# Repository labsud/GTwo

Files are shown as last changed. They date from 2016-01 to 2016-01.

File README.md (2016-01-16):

<h1 id="gtwo_shield_for_arduino_due_tinyg_2">GTwo Shield for Arduino DUE &amp; TinyG 2</h1>

<p><a href="https://github.com/synthetos/TinyG">TinyG</a> is a 6 axis motion control system designed by Synthetos for driving CNC, Laser cutters, ans so on. It have been designed to run on Atmel ATxmega192. It&#8217;s a complete system (hard + soft).</p>

<p>Some faeatures : </p>

<ul>
<li>6 axis motion (XYZABC axes)</li>
<li>jerk controlled motion for acceleration planning (3rd order motion planning)</li>
<li>status displays (&#8216;?&#8217; character)</li>
<li>XON/XOFF and RTS/CTS protocol over USB serial</li>
<li>RESTful interface using JSON</li>
</ul>

<p><a href="https://github.com/synthetos/g2">TinyG 2</a> is a TinyG ARM port, also developed by Synthetos, working on Atmel Arm Processors, like the one used on low cost Arduino DUE. That port can be configured for using GRBL shields (Arduino Uno form factor) but unfortunately, pinout is slightly differents, so there&#8217;s no way to have more than 3 motors running. No commands, no emergency stops, spindle or homing&#8230; </p>

<p>GTwo is a shield designed to allow easy use or the port of TinyG with all functionnalities. </p>

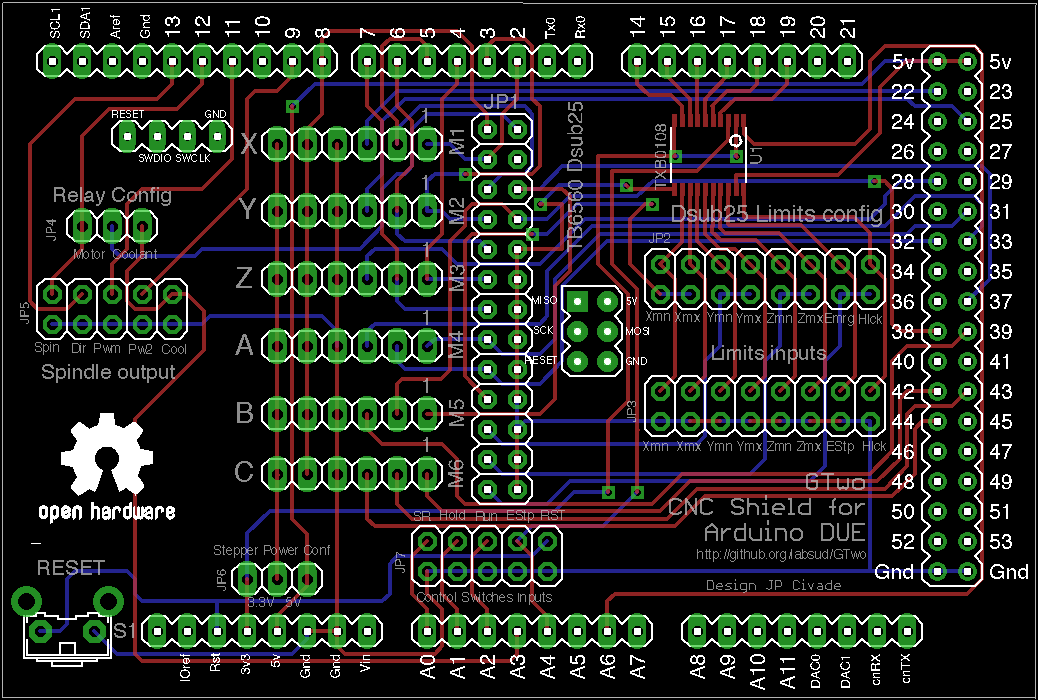
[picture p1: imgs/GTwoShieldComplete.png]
GTwo assembly


<p>That shield can be used :</p>

<ul>
<li>Directly connected to a <a href="https://www.google.fr/search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">TB 6560 &#8220;Red&#8221;</a>, for a maximum of 4 axis (X,Y,Z,A) and 4 GPIO inputs (I.E. homing X,Y,Z and emergency stop)</li>
<li>Connected thru 6 X 6 pins connectors to discrete drivers like Leadshine, Gekko, etc., allowing up to 6 axis (X,Y,Z,A,B,C).</li>
</ul>

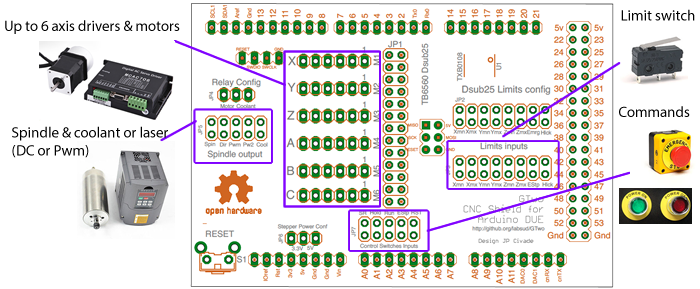
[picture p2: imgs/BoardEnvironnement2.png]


<h4 id="caracteristics">Caracteristics</h4>

<ul>
<li>Mostly passive shield, with all connectors for connecting spindle, PWM Spindle, coolant, homing &amp; Limits, switch for program control, up to 6 axis stepper driver boards</li>
<li>Since DUE is not 5V tolerant, limits inputs are level translated to be used @5V</li>
<li>All other inouts ARE not, and should no be connected to anything else than a 0V. (program control)</li>
</ul>

<h4 id="connections">Connections</h4>

<h5 id="when_using_a_tb6560_power_board_">When using a TB6560 power board :</h5>

That work is the property of Jean-Philippe Civade (jp at civade dot com) and is shared under <a href="licence-CC-By-NC 3.0.txt">Creative Common NonCommercial 3.0</a>

<ul>
<li>JP1 : For connectig to a TB6560 &#8220;Red&#8221; Stepper driver board. A cable must be made with a HE10-26F > DB25F emulating parallel port. If using JP1, don&#8217;t use M1>M6</li>
<li>JP2 : Limits configuration for TB6560. Must be left unequipped if using M1 > M6 connections.</li>
<li>JP4 : Relay config. Must be left unequipped if using M1 > M6 connections.</li>
</ul>

<h5 id="when_using_m1_m6_connections_to_discrete_drivers">When using M1 > M6 connections to discrete drivers</h5>

<ul>
<li>M1 > M6 : Allows to connect up to 6 steppers motors (X/Y/Z/A/B/C). If using M1>M6, don&#8217;t use JP1.</li>
<li>JP3 : Limits inputs. Allow to connect limit and/or homing switches (X-, X+, Y-, Y+, Z-, Z+), emergency stop and optionnaly Hardware interlock. All inputs are 5V tolerant.</li>
<li>JP6 : Stepper power conf </li>
</ul>

<p>M1 to M6 pinout :
* Broche 1 : Step
* Broche 2 : Dir
* Broche 3 : Enable motor (independant enable for each axis)
* Broche 4 : GND
* Broche 5 : Global Enable for all axis
* Broche 6 : VCC (3.3V or 5V depending of JP6) setting</p>

<h5 id="other_connectors_">Other connectors :</h5>

<ul>
<li>JP5 : Spindle &amp; Coolant outputs (3.3V). &#8220;Spindle&#8221; is for Spindle on/off, &#8220;dir&#8221; is for spindle direction (CW/CCW), &#8220;PWM&#8221; is for connecting a PWM spindle, &#8220;PW2&#8221; is an optionnal secondary PWM, &#8220;Cool&#8221; is for connecting cooolant command. </li>
<li>JP7 : Control inputs. Connect swtches for Soft Reset (SR), Feed Hold (Hold), Cycle Start (Run), Emergency Stop (ESTP) or hardware reset (RST)</li>
</ul>

<h5 id="configuration_jumpers_">Configuration Jumpers :</h5>

<p>JP2 : Must be equipped with 4 jumpers allowing to route X- or X+ to Pin 10 of parallel port, Y- or Y+ to pin 11 of parallel port, Z-or Z+ on pin 12 of paralel port, and emergency stop or hardware interlock on pin 13 of parallel port. 
JP4 : Must be equipped with 1 jumper allowing to route motor or coolant to the embedded relay of TB6560 red board.
JP6 : Must be equipped with 1 jumper to route a 3.3V or a 5V to M1 > M6 pin 6.</p>

<h5 id="associated_documents_">Associated Documents :</h5>

<ul>
<li><a href="GTwoShieldSchematics.pdf">Schematics</a></li>
<li><a href="partlist.txt">BOM</a></li>
<li><a href="GTwoShield.zip">ZIP archive for manufacturing</a></li>
<li><a href="imgs/DUE tinyG2 pinout 0.2.pdf">Due Pinout for Tiny G2</a></li>
<li><a href="imgs/GTwoShieldAssembly.pdf">Assembly</a></li>
<li><a href="imgs/GTwoShieldTop.png">Top view</a></li>
<li><a href="imgs/GTwoShieldBottom.png">Bottom view</a></li>
</ul>

<h5 id="example_configuration_">Example configuration :</h5>

<p>This configuration fits to a machine with origin switches at the bottom left ad top Z, for a CNC machine. GTtwo is connected to a TB6560 driver board, and board relay is used to power the spindle. (motor = M3/M5 Gcode). 
TB6560 inputs are Xmin, Ymin, ZMax, Emergency stop. A 3.3V is routed to M1>M6 pin 6.</p>

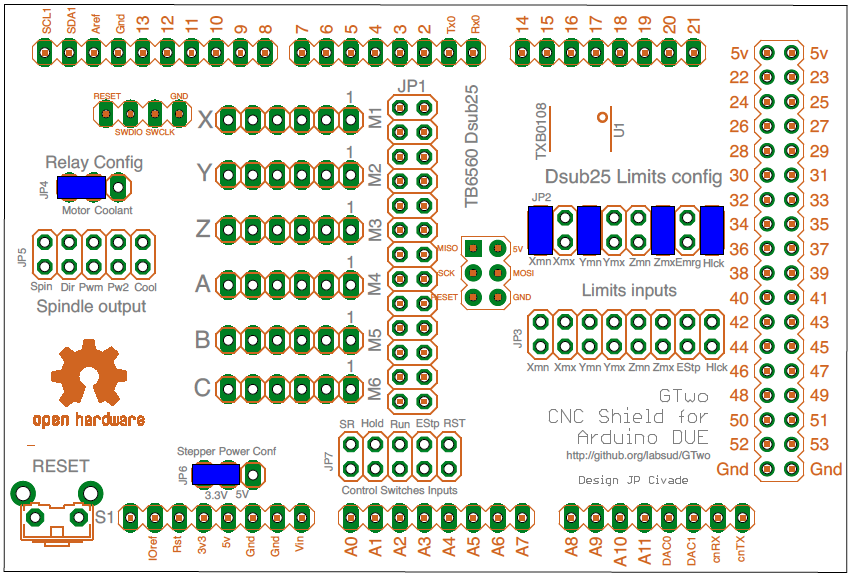
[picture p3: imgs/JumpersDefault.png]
GTwo Default Configuration


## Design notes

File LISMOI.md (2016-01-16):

<h1 id="shield_gtwo_pour_arduino_due_tinyg_2">Shield GTwo pour Arduino DUE &amp; TinyG 2</h1>

Ce travail est la propri&eacute;t&eacute; de Jean-Philippe Civade (jp at civade dot com), et est mis sous licence <a href="licence-CC-By-NC 3.0.txt">Creative Common NonCommercial 3.0</a>

<p><a href="https://github.com/synthetos/TinyG">TinyG</a> est un syst&egrave;me de contr&ocirc;le &agrave; 6 axes d&eacute;velopp&eacute;  par Synthetos pour piloter CNC, d&eacute;coupe laser, etcc. Il a &eacute;t&eacute; con&ccedil;u pour fonctionner sur processeur Atmel ATxmega192.  C&#8217;est un syst&egrave;me complet (hard + soft).</p>

<p>Quelques caract&eacute;ristiques :</p>

<ul>
<li>Gestion de 6 axes (XYZABC)</li>
<li>Planification de mouvement du 3e ordre </li>
<li>Affichage des &eacute;tats (caract&egrave;re &#8216;?&#8217;)</li>
<li>Gestion des protocoles de handshake XON/XOFF &amp; RTS/CTS sur la liaison s&eacute;rie via USB </li>
<li>Interface RESTful utilisant JSON</li>
</ul>

<p><a href="https://github.com/synthetos/g2">TinyG 2</a> est un portage de TinyG sur processeurs ARM, d&eacute;velopp&eacute; &eacute;galement par Synthetos, fonctionnant sur les processeurs ARM d&#8217;Atmel, comme celui utilis&eacute; sur la carte &eacute;conomique Arduino DUE. Ce portage peut &ecirc;tre configur&eacute; pour utilis&eacute; des shields GRBL standard (format Arduino UNO), mais malheureusement pas compl&egrave;tement. En effet, si il est possible de commander les moteurs pas &agrave; pas, tous les autres signaux sont rout&eacute;s sur les connecteurs d&#8217;extension de la l&#8217;Arduino mega, ce qui rend inaccessible les commandes manuelles, de fins ds courses, de commande de broche, etc.. </p>

<p>C&#8217;est pr&eacute;cis&eacute;ment pour rendre accessible tous ces signaux qu&#8217;a &eacute;t&eacute; d&eacute;velopp&eacute; la shield GTwo: Permettre une utilisation facile de TinyG2 avec toutes les fonctionnalit&eacute;s mat&eacute;rielles disponibles. </p>

<p>GTwo assembly</p>

<p>Cette shield peut &ecirc;tre utilis&eacute;e de 2 fa&ccedil;ons :</p>

<ul>
<li>Raccord&eacute;e directement &agrave; une carte de puissance <a href="https://www.google.fr/search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">TB 6560 &#8220;Rouge&#8221;</a>. Cela permet la commande d&#8217;un maximum de 4 axes (X,Y,Z,A) et l&#8217;usage de 4 entr&eacute;es GPIO (exemple : Prise d&#8217;origine machine X,Y,Z et arr&ecirc;t d&#8217;urgence)</li>
<li>Raccord&eacute;e &agrave; des contr&ocirc;leurs d&#8217;axes ind&eacute;pendants (Leadshine, Gekko, etc.,) via des connecteurs &agrave; 6 broches. C&#8217;est dans ce cas jusqu&#8217;&agrave; 6 axes qui peuvent &ecirc;tre pilot&eacute;s (X,Y,Z,A,B,C). Dans ce cas, jusqu&#8217;&agrave; 6 swiches d&#8217;origine machine ou de fin de course peuvent &ecirc;tre raccord&eacute;es.</li>
</ul>

<p>GTwo assembly</p>

<h4 id="caracteristiques">Caracteristiques</h4>

<ul>
<li>Shield principalement passive, avec tous les connecteurs pour connecter broche traditionnelle ou PWM, arrosage, switches de prise d&#8217;origine et de limites, boutons de commande de l&#8217;ex&eacute;cution du programme, et jusqu&#8217;&agrave; 6 axes via des drivers externes.</li>
<li>Du fait que l&#8217;Arduino DUE n&#8217;est pas tol&eacute;rante au 5V (3.3V seulement&#8230;), un level shifter &agrave; 8 canaux est int&eacute;gr&eacute; pour permettre le raccordement des fins de courses en 5V (fins de courses actifs)</li>
<li>Toutes les autres entr&eacute;es (contr&ocirc;le de l&#8217;ex&eacute;cution du programme) sont pr&eacute;vues pour &ecirc;tre raccord&eacute;es au 0V via des interrupteurs et ne devraient jamais &ecirc;tre raccord&eacute;es &agrave; un 5V sous peine de destruction de l&#8217;Arduino DUE.</li>
</ul>

<h4 id="connexions">Connexions</h4>

<h5 id="lorsque_raccorde_une_carte_de_puissance_tb6560_8220rouge8221_">Lorsque raccord&eacute;e &agrave; une carte de puissance TB6560 &#8220;Rouge&#8221; :</h5>

<ul>
<li>JP1 : Raccordement &agrave; l&#8217;entr&eacute;e parall&egrave;le de la carte de puissance TB6560 &#8220;Rouge&#8221; via un cable r&eacute;alis&eacute; avec un connecteur HE10/26 points > Sub D 25 broches femelle. Si ce connecteur est utilis&eacute;, ne pas utiliser M1>M6</li>
<li>JP2 : Configuration des limites pour TB6560. Ne pas &eacute;quiper lors de l&#8217;utilisation de M1 > M6.</li>
<li>JP4 : Configuration du relais de la TB6560. Ne pas &eacute;quiper lors de l&#8217;utilisation de M1 > M6.</li>
</ul>

<h5 id="lorsque_raccorde_des_drivers_moteurs_externes_via_m1_m6">Lorsque raccord&eacute;e &agrave; des drivers moteurs externes via  M1 &agrave; M6</h5>

<ul>
<li>M1 > M6 : Permet de raccorder jusqu&#8217;&agrave; 6 drivers pour moteurs pas &agrave; pas ou servo moteurs (X/Y/Z/A/B/C). Si utilis&eacute;, ne pas utiliser JP1.</li>
<li>JP3 : Entr&eacute;es limites. Permet de raccorder les interrupteurs de d&eacute;tection de prise d&#8217;origine et de limite.(X-, X+, Y-, Y+, Z-, Z+), l&#8217;arr&ecirc;t d&#8217;urgence et l&#8217;interrupteur capot ouvert. Toutes les entr&eacute;es sont compatibles 5V.</li>
<li>JP6 : Configuration de l&#8217;alimentation envoy&eacute;e sur M1>M6 </li>
</ul>

<p>Le brochage des connecteurs M1 &agrave; M6 est le suivant :
* Broche 1 : Pas (Step)
* Broche 2 : Direction (Dir)
* Broche 3 : Activation moteur (Enable, pour chaque moteur)
* Broche 4 : GND
* Broche 5 : Activation globale (Global Enable pour tous les moteurs simultan&eacute;ment)
* Broche 6 : VCC (3.3V ou 5V en fonction de JP6)</p>

<h5 id="autres_connecteurs_">Autres connecteurs :</h5>

<ul>
<li>JP5 : Sortie broche et arrosage (3.3V). &#8220;Spindle&#8221; est pour le M/A broche, &#8220;dir&#8221; est pour le sens de rotation de la broche, &#8220;PWM&#8221; est pour raccorder une broche &agrave; contr&ocirc;le de vitesse en modulation de largeur d&#8217;impulsion, &#8220;PW2&#8221; est un PWM secodaaire  et &#8220;Cool&#8221; est pour raccorder la commande d&#8217;arrosage.</li>
<li>JP7 : Entr&eacute;es de contr&ocirc;le de l&#8217;ex&eacute;cution du programme. Y raccorder des poussoirs pour  le Reset Soft (SR), la suspension du programme, La reprise ou le d&eacute;marrage du programme (Run),l&#8217;arr&ecirc;t d&#8217;urgence (ESTP) ou le reset mat&eacute;riel de la carte (RST)</li>
</ul>

<h5 id="cavaliers_de_configuration">Cavaliers de configuration:</h5>

<p>JP2 : (si utilisation de la TB6560 rouge) Doit &ecirc;tre &eacute;quip&eacute; de 4 cavaliers permettant le routage des switches de prise d&#8217;origine machine  X- ou X+ sur la broche Pin 10 du port parall&egrave;le, Y- ou Y+ &agrave; la broche 11 du port parall&egrave;le, Z-ou Z+ &agrave; la broche 12 du port parall&egrave;le, l&#8217;arr&ecirc;t d&#8217;urgence ou la protection capot ouvert &agrave; la broche 13 du port parall&egrave;le. 
JP4 : (si utilisation de la TB6560 rouge) Doit &ecirc;tre &eacute;quip&eacute; d&#8217;un cavalier permettant de router la commande moteur ou la commande d&#8217;arrosage sur le relais int&eacute;gr&eacute;.
JP6 : (si utilisation des connecteurs M1 &agrave; M6) Doit &ecirc;tre &eacute;quip&eacute; d&#8217;un cavalier permettant d&#8217;envoyer 3.3V ou 5V &agrave; la broche 6 des connecteurs M1 &agrave; M6.</p>

<h5 id="documents_joints_">Documents joints :</h5>

<ul>
<li><a href="GTwoShieldSchematics.pdf">Sch&eactute;ma de principe</a></li>
<li><a href="partlist.txt">Nomenclature</a></li>
<li><a href="GTwoShield.zip">Archive Zip pour la fabrication</a></li>
<li><a href="imgs/DUE tinyG2 pinout 0.2.pdf">Brochage de la Due avec Tiny G2</a></li>
<li><a href="imgs/GTwoShieldAssembly.pdf">Assemblage</a></li>
<li><a href="imgs/GTwoShieldTop.png">Dessus</a></li>
<li><a href="imgs/GTwoShieldBottom.png">Dessous</a></li>
</ul>

<h5 id="exemple_de_configuration">Exemple de configuration:</h5>

<p>Cette configuration correspond &agrave; une machine dont les swiches d&#8217;origine sont en bas &agrave; gauche et en haut du Z, pour une machine de CNC. GTtwo est dans ce cas raccord&eacute;e &agrave; une carte de puissance TB6560 &#8220;rouge&#8221; dont le relais est utilis&eacute; pour commander le M/A d&#8217;une broche  (moteur on /off = Commandes Gcode M3/M5). 
Les entr&eacute;es de la TB6560 sont respectivement raccord&eacute;es &agrave; Xmin, Ymin, ZMax et un bouton d&#8217;arr&ecirc;t d&#8217;urgence. Une alimentation 3.3V is rout&eacute;e vers la broche 6 des connecteurs M1 &agrave; M6 qui sont inutilis&eacute;s.</p>

<p>GTwo Default Configuration</p>

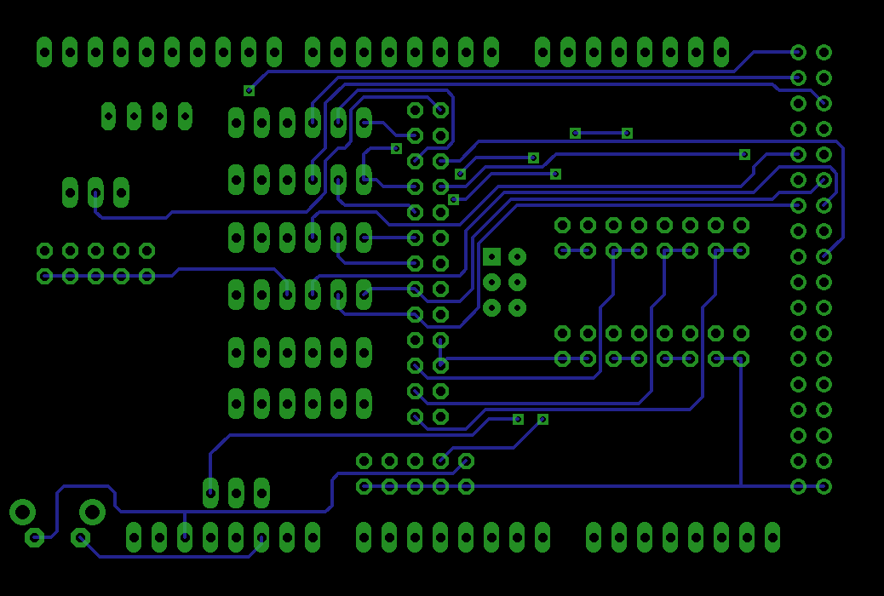
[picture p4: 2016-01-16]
imgs/GTwoShieldBottom.png

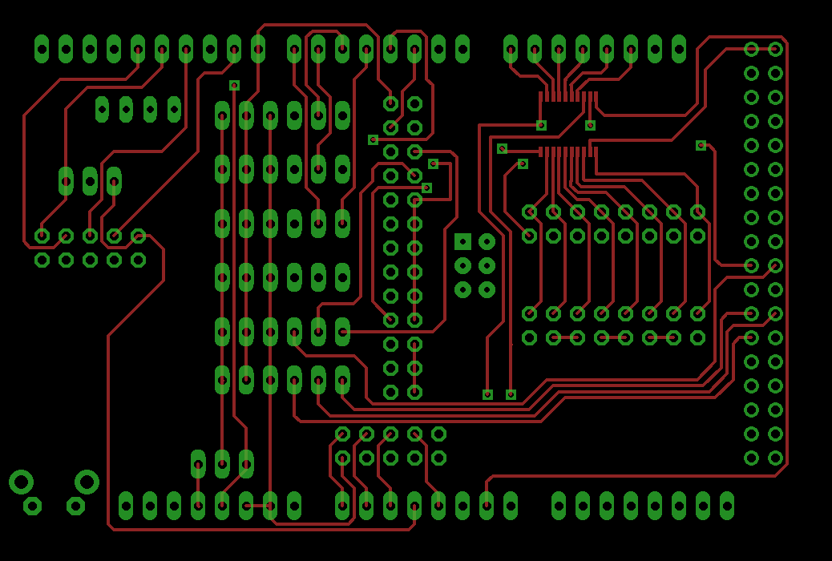
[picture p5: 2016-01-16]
imgs/GTwoShieldTop.png

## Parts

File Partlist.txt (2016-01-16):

Part     Value                   Package     Library      Position (inch)       Orientation

JP1      Header 2 rows           2X13        pinhead      (1.9 1.575)           R270
JP2      Header 2 rows           2X08        pinhead      (2.775 1.675)         R0
JP3      Header 2 rows           2X08        pinhead      (2.775 1.25)          R0
JP4      Header 1 row            1X03        pinhead      (0.6 1.85)            R0
JP5      Header 2 rows           2X05        pinhead      (0.6 1.575)           R0
JP6      Header 1 row            1X03        pinhead      (1.15039998 0.675)    R180
JP7      Header 2 rows     	   2X05        pinhead      (1.85 0.75)           R0
M1       Header 1 row            1X06        pinhead      (1.4 2.125)           R180
M2       Header 1 row            1X06        pinhead      (1.4 1.9)             R180
M3       Header 1 row            1X06        pinhead      (1.4 1.675)           R180
M4       Header 1 row            1X06        pinhead      (1.4 1.45)            R180
M5       Header 1 row            1X06        pinhead      (1.4 1.225)           R180
M6       Header 1 row            1X06        pinhead      (1.4 1.025)           R180
S1       Pushbutton              B3F-31XX    adafruit     (0.45 0.55)           R0
U1       TXB0108                 TSSOP20                  (2.58810002 2.08770005)

6 X 2.54mm Jumpers
1 X HE10 26 pins (TB6560 option)
1 X DB25 Femelle (TB6560 Option)
1 X 5cm 26 pin ribbon

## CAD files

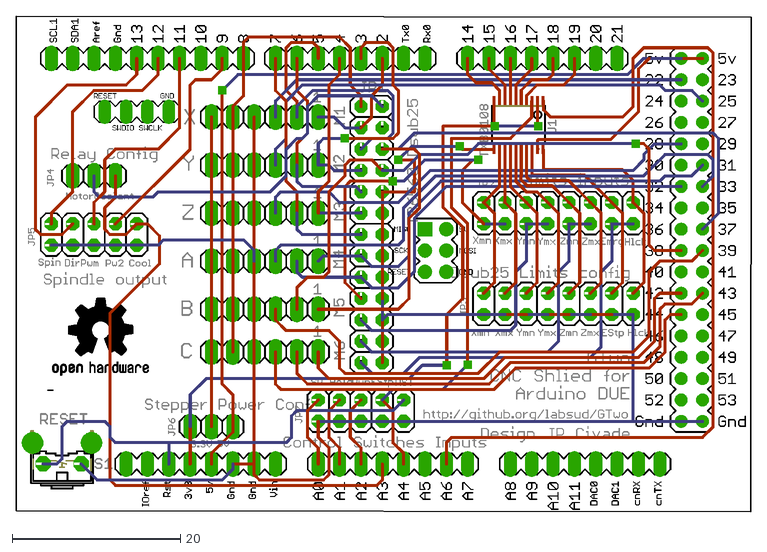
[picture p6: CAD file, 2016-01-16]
GTwoShield.dxf
87.4 x 58.9

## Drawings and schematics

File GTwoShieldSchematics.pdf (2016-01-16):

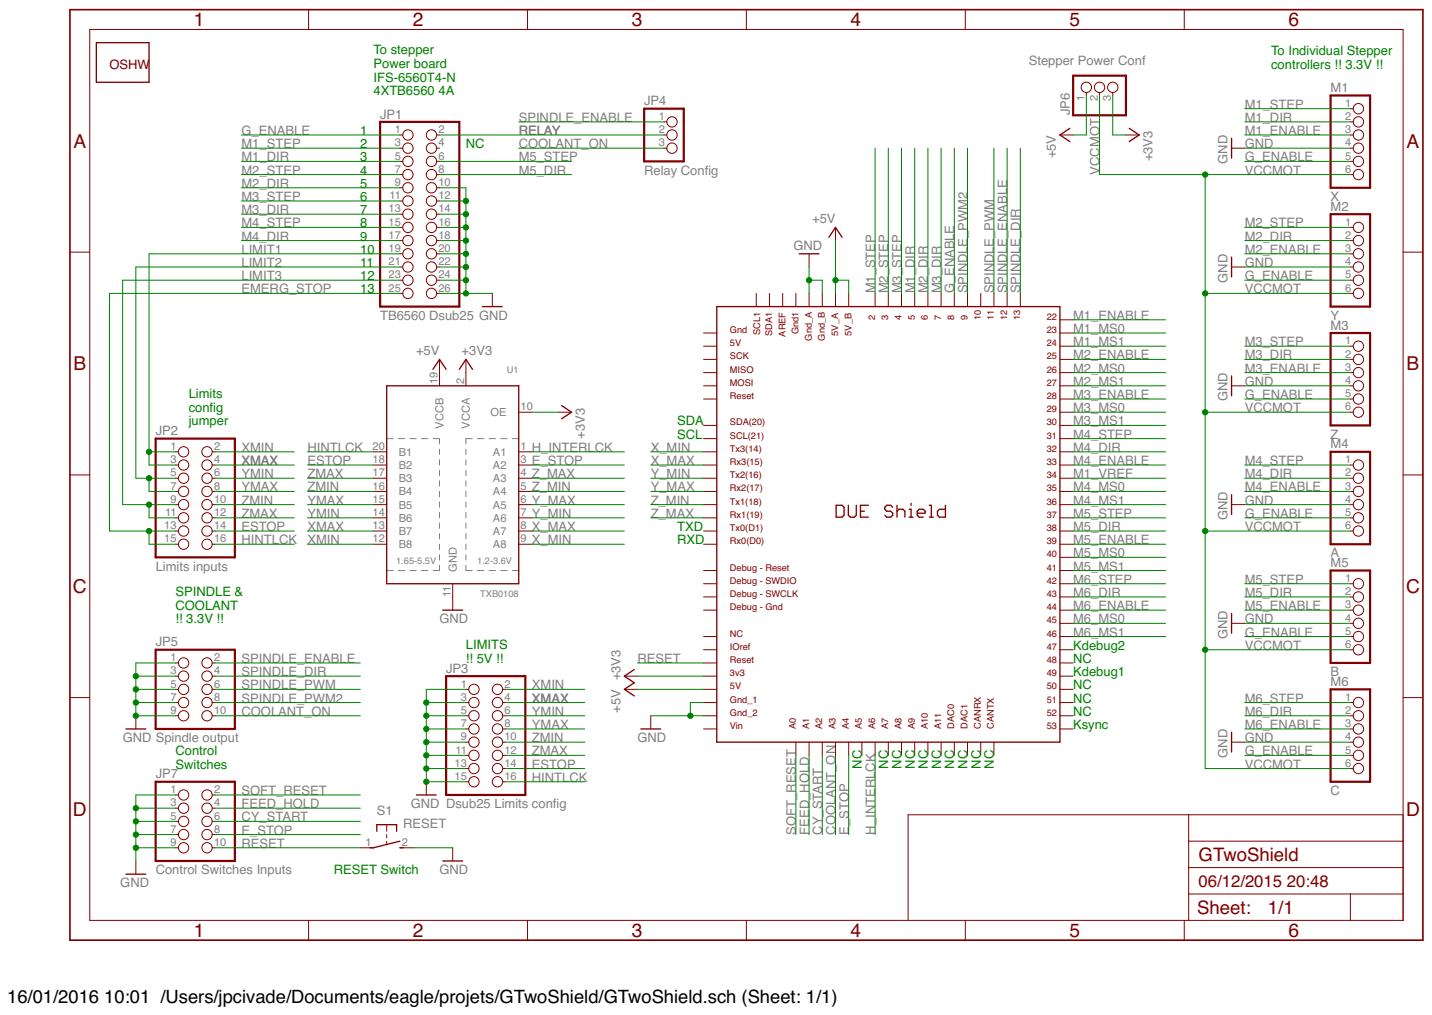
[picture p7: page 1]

To stepper Power board

To Individual Stepper controllers !! 3.3V !!

GND GND GND GND GND

SDA1 SCL1 Debug - Reset Debug - Gnd Debug - SWDIO
5VGnd

16/01/2016 10:01 /Users/jpcivade/Documents/eagle/projets/GTwoShield/GTwoShield.sch (Sheet: 1/1)

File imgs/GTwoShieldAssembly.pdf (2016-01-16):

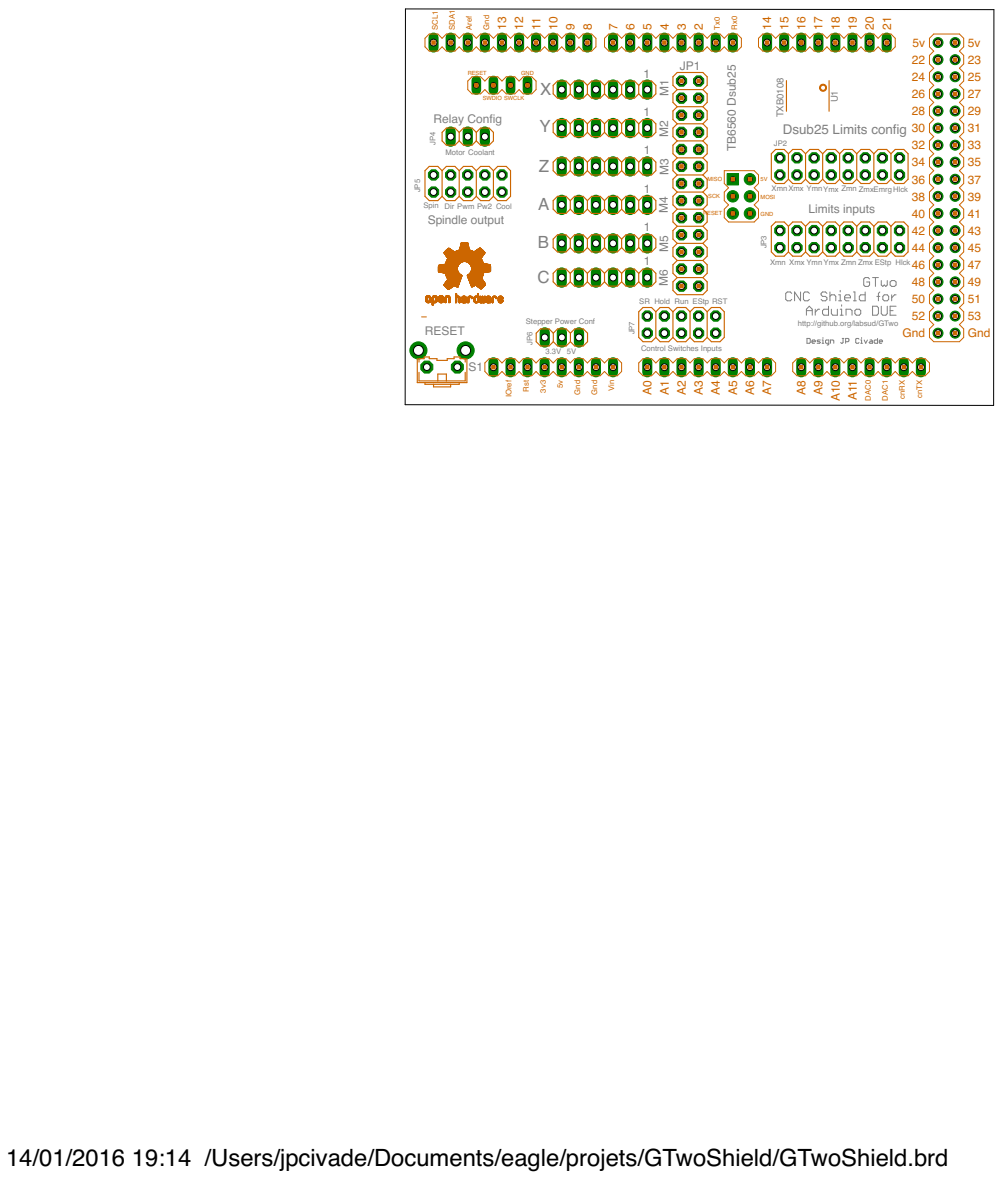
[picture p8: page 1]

5VGND
XmnXmx YmnYmx Zmn ZmxEmrg

SR Hold Run EStp RST

Stepper Power Conf RESET

http://github.org/labsud/GTwo

14/01/2016 19:14 /Users/jpcivade/Documents/eagle/projets/GTwoShield/GTwoShield.brd

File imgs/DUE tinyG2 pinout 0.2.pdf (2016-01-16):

# tinyG2 add-on WIP

# tinyG2

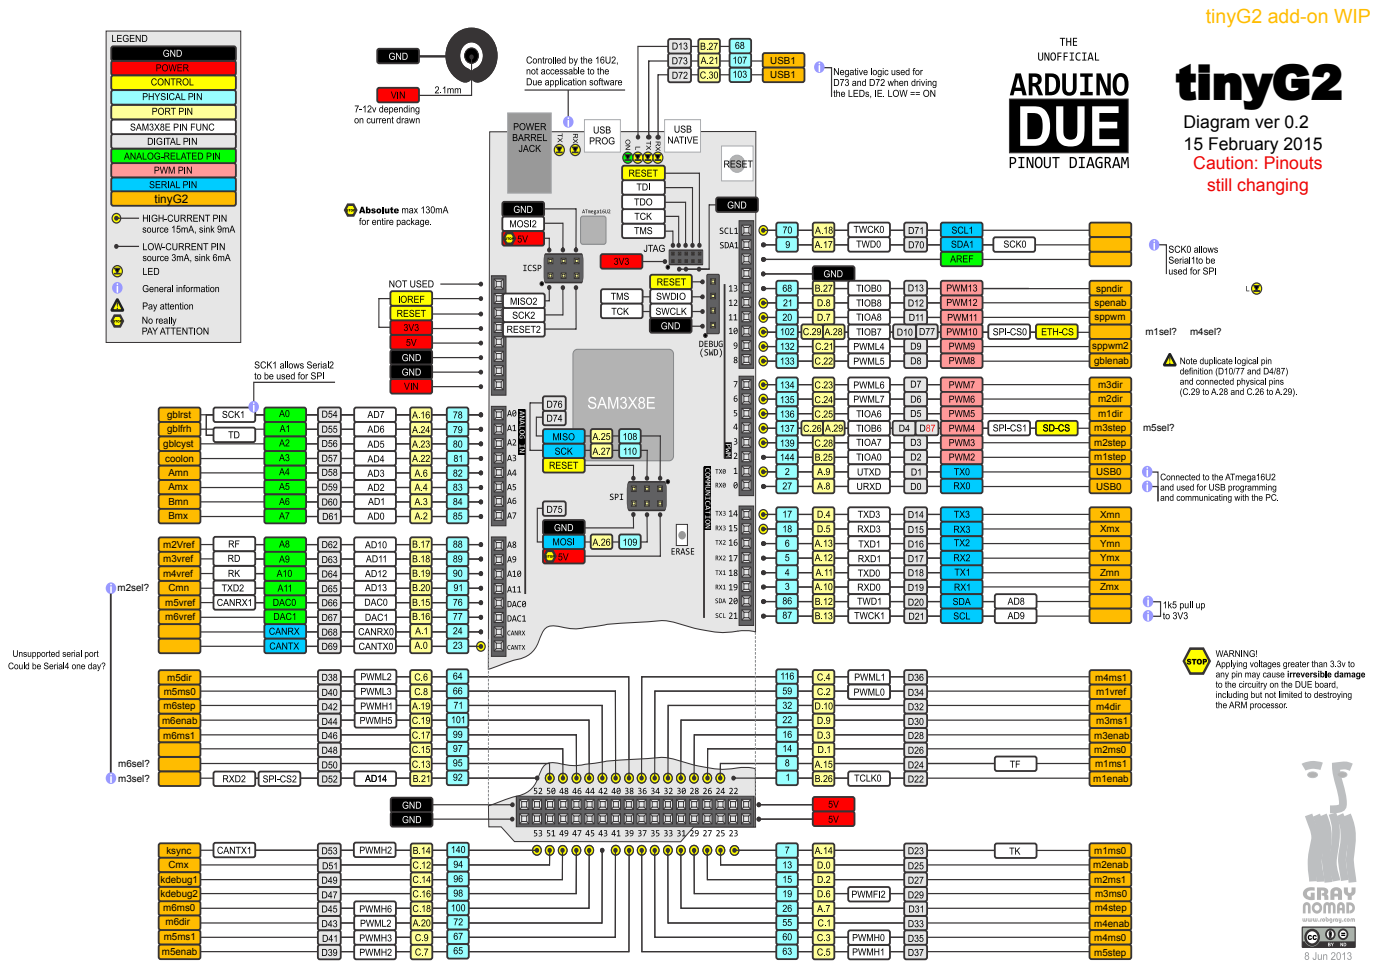
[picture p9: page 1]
Xmn Xmx Ymn Ymx Zmn Zmx; Amn Amx Bmn Bmx; Cmx; Cmn; gblrst gblfrh gblcyst coolon; m2Vref m3vref m4vref; m5vref m6vref; m5dir m5ms0 m6step m6enab m6ms1; m6sel? m3sel?; spndir spenab sppwm; m1sel?; sppwm2 gblenab; m3dir m2dir m1dir m3step m2step m1step USB0; m4ms1 m1vref m4dir m3ms1 m3enab m2ms0 m1ms1 m1enab; m1ms0 m2enab m2ms1 m3ms0 m4step m4enab m4ms0 m5step; m2sel?; m4sel?; m5sel?; m5enab; m6dir; kdebug2; kdebug1; ksync; USB0; USB1 USB1; tinyG2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

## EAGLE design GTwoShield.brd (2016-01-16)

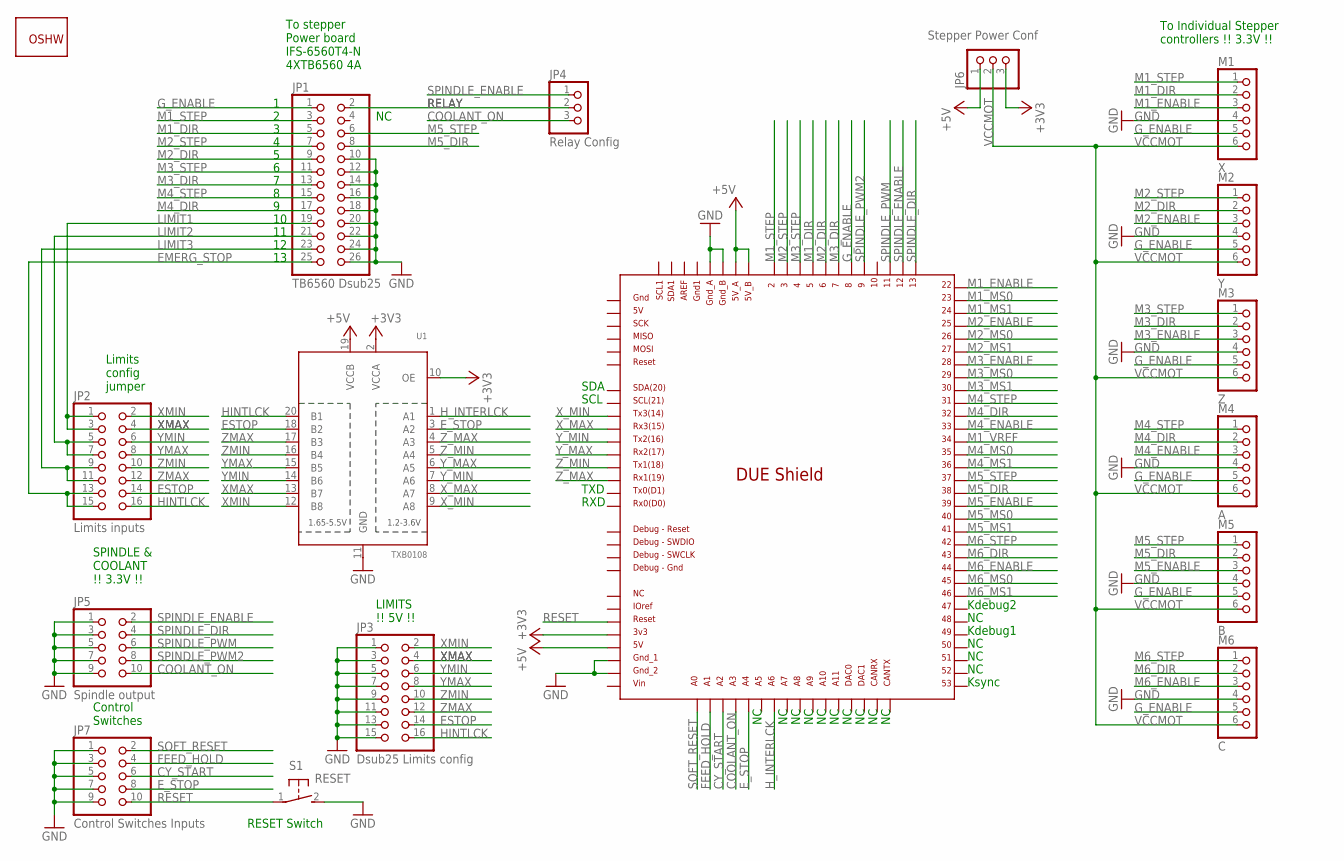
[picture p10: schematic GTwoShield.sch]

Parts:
GOLD_ORB_SM1: OSHWLOGO_GOLD_ORB_MED; OSHW1
JP1: TB6560 Dsub25; 2X13
JP2: Limits inputs; 2X08
JP3: Dsub25 Limits config; 2X08
JP4: Relay Config; 1X03
JP5: Spindle output; 2X05
JP6: Stepper Power Conf; 1X03
JP7: Control Switches Inputs; 2X05
M1: X; 1X06
M2: Y; 1X06
M3: Z; 1X06
M4: A; 1X06
M5: B; 1X06
M6: C; 1X06
S1: RESET; B3F-31XX
U1: TXB0108; TSSOP20
U$1: DUE(NORMAL)

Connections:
+3V3: JP6.3, U1.2 (VCCA), U1.10 (OE), U$1.3V3
+5V: JP6.1, U1.19 (VCCB), U$1.5V, U$1.5V_A, U$1.5V_B
COOLANT_ON: JP4.3, JP5.10, U$1.A3
CY_START: JP7.6, U$1.A2
EMERG_STOP: JP1.25, JP2.13, JP2.15
ESTOP: JP2.14, JP3.14, U1.18 (B2)
E_STOP: JP7.8, U1.3 (A2), U$1.A4
FEED_HOLD: JP7.4, U$1.A1
GND: JP1.10, JP1.12, JP1.14, JP1.16, JP1.18, JP1.20, JP1.22, JP1.24, JP1.26, JP3.1, JP3.3, JP3.5, JP3.7, JP3.9, JP3.11, JP3.13, JP3.15, JP5.1, JP5.3, JP5.5, JP5.7, JP5.9, JP7.1, JP7.3, JP7.5, JP7.7, JP7.9, M1.4, M2.4, M3.4, M4.4, M5.4, M6.4, S1.2 (S), U1.11 (GND), U$1.GND_1, U$1.GND_2, U$1.GND_A, U$1.GND_B
G_ENABLE: JP1.1, M1.5, M2.5, M3.5, M4.5, M5.5, M6.5, U$1.8
HINTLCK: JP2.16, JP3.16, U1.20 (B1)
H_INTERLCK: U1.1 (A1), U$1.A6
LIMIT1: JP1.19, JP2.1, JP2.3
LIMIT2: JP1.21, JP2.5, JP2.7
LIMIT3: JP1.23, JP2.9, JP2.11
M1_DIR: JP1.5, M1.2, U$1.5
M1_ENABLE: M1.3, U$1.22
M1_MS0: U$1.23
M1_MS1: U$1.24
M1_STEP: JP1.3, M1.1, U$1.2
M1_VREF: U$1.34
M2_DIR: JP1.9, M2.2, U$1.6
M2_ENABLE: M2.3, U$1.25
M2_MS0: U$1.26
M2_MS1: U$1.27
M2_STEP: JP1.7, M2.1, U$1.3
M3_DIR: JP1.13, M3.2, U$1.7
M3_ENABLE: M3.3, U$1.28
M3_MS0: U$1.29
M3_MS1: U$1.30
M3_STEP: JP1.11, M3.1, U$1.4
M4_DIR: JP1.17, M4.2, U$1.32
M4_ENABLE: M4.3, U$1.33
M4_MS0: U$1.35
M4_MS1: U$1.36
M4_STEP: JP1.15, M4.1, U$1.31
M5_DIR: JP1.8, M5.2, U$1.38
M5_ENABLE: M5.3, U$1.39
M5_MS0: U$1.40
M5_MS1: U$1.41
M5_STEP: JP1.6, M5.1, U$1.37
M6_DIR: M6.2, U$1.43
M6_ENABLE: M6.3, U$1.44
M6_MS0: U$1.45
M6_MS1: U$1.46
M6_STEP: M6.1, U$1.42
RELAY: JP1.2, JP4.2
RESET: JP7.10, S1.1, U$1.RESET
SOFT_RESET: JP7.2, U$1.A0
SPINDLE_DIR: JP5.4, U$1.13
SPINDLE_ENABLE: JP4.1, JP5.2, U$1.12
SPINDLE_PWM: JP5.6, U$1.11
SPINDLE_PWM2: JP5.8, U$1.9
VCCMOT: JP6.2, M1.6, M2.6, M3.6, M4.6, M5.6, M6.6
XMAX: JP2.4, JP3.4, U1.13 (B7)
XMIN: JP2.2, JP3.2, U1.12 (B8)
X_MAX: U1.8 (A7), U$1.RX3
X_MIN: U1.9 (A8), U$1.TX3
YMAX: JP2.8, JP3.8, U1.15 (B5)
YMIN: JP2.6, JP3.6, U1.14 (B6)
Y_MAX: U1.6 (A5), U$1.RX2
Y_MIN: U1.7 (A6), U$1.TX2
ZMAX: JP2.12, JP3.12, U1.17 (B3)
ZMIN: JP2.10, JP3.10, U1.16 (B4)
Z_MAX: U1.4 (A3), U$1.RX1
Z_MIN: U1.5 (A4), U$1.TX1

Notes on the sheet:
Kdebug2
Kdebug1
Ksync
SDA
SCL
TXD
RXD
To stepper Power board IFS-6560T4-N 4XTB6560 4A
Limits config jumper
To Individual Stepper controllers !! 3.3V !!
SPINDLE & COOLANT !! 3.3V !!
Control Switches
RESET Switch
LIMITS !! 5V !!

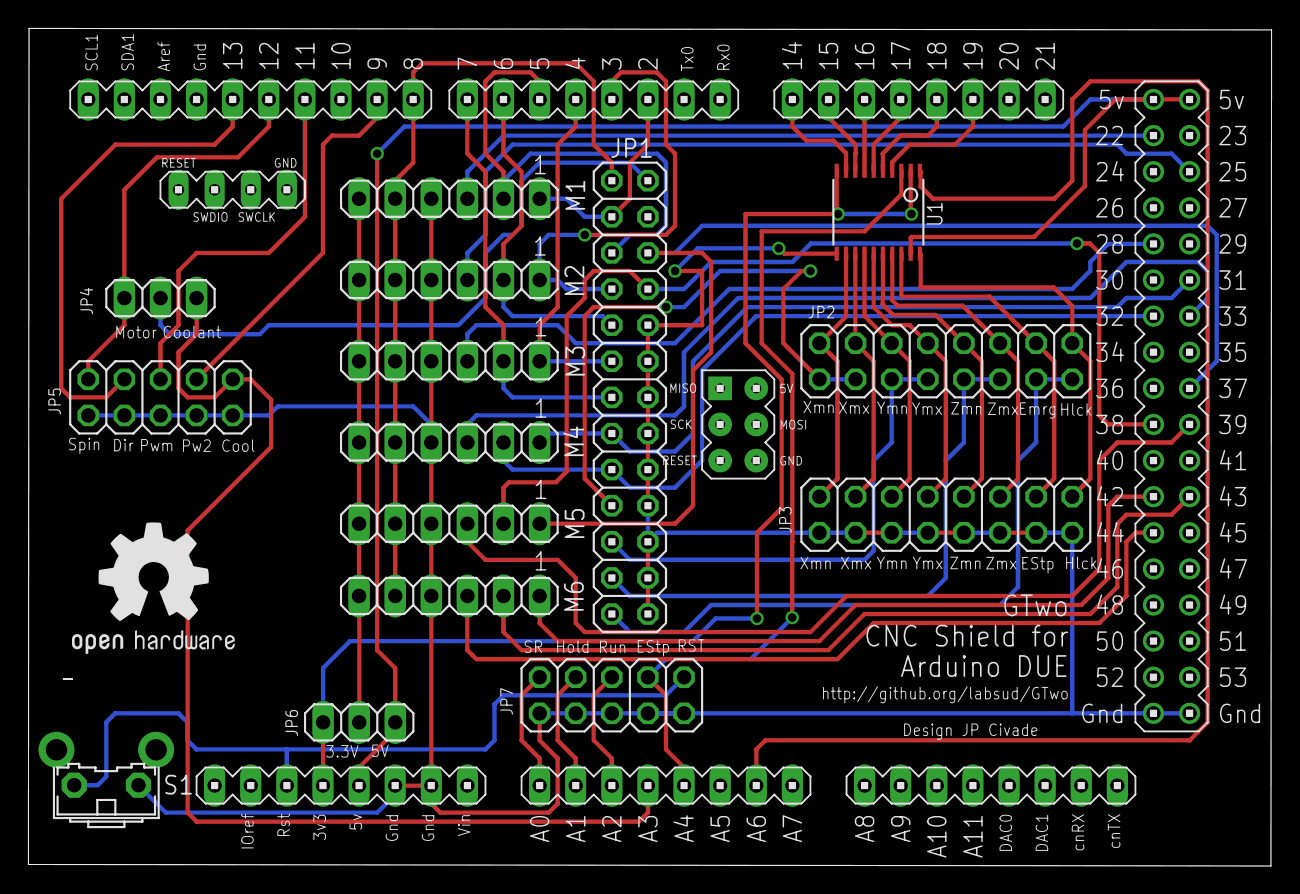
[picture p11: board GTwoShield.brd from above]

Board: 2 copper layers, 87.4 x 58.9 mm, 17 parts (0 on the bottom side), 53 nets.

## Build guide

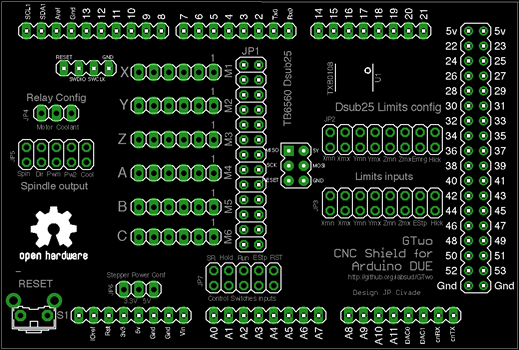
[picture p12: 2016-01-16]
imgs/GTwoShieldAssembly2.png

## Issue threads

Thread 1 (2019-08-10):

Thank you!

norru, 2019-08-10:
Hi @labsud,

I am trying to build my own CNC machine as a semicustom WorkBee design using the Due and g2core.

I was thinking of designing my own from scratch but found your work here instead, which looks like an awesome starting point.

I am planning to use inexpensive TB6600 drivers which require 5v signal levels. Due spits out 3.3v and although the TB6600 I intend to use may be tolerant to 3.3v inputs, I've read around that it's not good practice.

In your design I haven't seen any level shifting logic so I guess you went with the "drivers will be ok" mindset.

Did it work for you? Otherwise I might want to tweak your shield to add level shifting to the motor control pins.

Thanks
Nico

ewidance, 2019-08-11:
HI Nico

As you can see in the schematics (https://github.com/labsud/GTwo/blob/master/GTwoShieldSchematics.pdf) there is a bidirectional level translator, used for 6 endstops, interlock and Estop inputs. But it does not work properly for two reasons:
- Choosen translator is bidirectionnal, and use "less impendance" method to autodetermine witch pin is the input for a group of 4 inputs. Depending to what is connected to inputs, level translator can make a bad guess, reverting loginc.
- TinyG2 doens not have a proper debbounce logic. It is necessary to add an R/C circuit for making hardware debbouce.

Becasue that was a one shot project, i did not update the PCB on github, but my prototyê wa updated to remove the level translator and replace it with a R/C filter. I did not implement level shifting logic all my inputs where powered wit 3.3V.

Outputs are directly wrapped to stepper drivers. Yes, outputs could also be improved using for example non inverting buffers or level shifters for improving noise immunity and giving enough energy to opto on drivers.

I stopped to work with G2 when software team started to go to G2Core. This massive update broke almost totally usage. That was especially true for the modifications i've made (and suggested) for COreXY kinematic.

I did not recently used G2, and maybe 3 years after it is back to a working level...

Finally the machine used for G2 have been converted to GRBL STM32 (https://github.com/usbcnc/grbl and https://github.com/dungjk/grbl-stm32).

My final advice, would be first to carfully check status, bugs and fonctionning ov TinyG2 before developping a board...

Sincerely
JP CIVADE

TheAnsgar, 2022-01-15:
Hi,

do you know why the shield doesn't work anymore with g2core?

Kind regards
Ansgar
